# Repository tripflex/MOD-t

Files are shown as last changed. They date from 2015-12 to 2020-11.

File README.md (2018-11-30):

New Matter MOD-t 3d Printer Repo
================================

This repository is a collection of files (firmware, test files, configurations, etc) for the NewMatter MOD-t 3d Printer.

**WARNING:** I take absolutely no responsibility for anything you do with these files or instructions, play at your own risk!

MOD-t's Anonymous
---------------
As of February 28, 2018, New Matter has closed its doors and will no longer be providing WiFi connectivity to the MOD-t through the New Matter Store (will be open until Summer 2018).  A few of us that still enjoy our MOD-t have created a Slack group, please feel free to join us if you need help or want to discuss the future of the MOD-t

Unfortunately New Matter has decided to not release any of the source code for the MOD-t, as well as any software, [stating that there's licensed code they can't release](https://www.reddit.com/r/newmatter/comments/7xly0q/request_for_unewmatter_open_source_modt_firmware/), so instead of providing anything they could without licensed code, they provided nothing ... so time to start reverse engineering, **accepting all applications :)**

[Join the MOD-t Users Slack Channel](https://join.slack.com/t/modt-users/shared_invite/enQtMzM4NzI5Mzg2NDY0LTYxZjUyZTNmNGFjNGZmZmVlOWY5NjNhM2E1MTlhYWY0MTc1YTgyYmMwZGRjNTVmMTI0MGUwNzliYTBmYjVjYmU)

[View NewMatter Subreddit](https://www.reddit.com/r/newmatter/)

[New Matter Closing Blog Post](https://newmatter.com/blog/permanent-closure/)
[Archive.org Cached Version](https://web.archive.org/web/20180301202219/https://newmatter.com/blog/permanent-closure/)

FINAL SOFTWARE WARNINGS
-----------------------
Under the software section you will find a `.dmg` for OSX and `.exe` for Windows that is the last and final software version released by New Matter. **BEWARE** if you install this version **and** upgrade the firmware through the software, this **WILL COMPLETELY DISABLE WIFI ON YOUR MOD-T**

How to print without New New Matter Store
-----------------------------------------
To convert your 3D files into G-code, we recommend two options: Cura, a free software-based slicer, and Astroprint.com, a web-based slicer.

We have prepared a [post on our blog that outlines the entire process for creating G-code with Cura and sending it to your MOD-t through our desktop software application (Web Archive Version)](https://web.archive.org/web/20180301201538/https://newmatter.com/blog/how-to-use-cura-with-the-mod-t/).

[http://www.robosupportsnewmatter.com/blog/how-to-use-cura-with-the-mod-t](http://www.robosupportsnewmatter.com/blog/how-to-use-cura-with-the-mod-t)

Users who prefer not to download and install Cura can continue to “slice” their 3D designs into G-code through a website called Astroprint. This option has the benefit of being web-based, meaning there is no software to download, install, or configure. For a more detailed look at the process for converting your 3D files into G-code using Astroprint, [please see this video](https://www.youtube.com/watch?v=UL1-fpE6NUI).

MOD-t Details
-------------

```
Bed Shape: Rectangular
X Axis: 155.4 mm
Y Axis: 104.6 mm
Z Axis: 130 mm

Nozzle Diameter: 0.4mm
Number of Extruders: 1
Heated Bed: FALSE
```

---

Files
-----

### [`Astroprint.md`](https://github.com/tripflex/MOD-t/tree/master/Astroprint.md)

Information on setting up/configuring Astroprint (with GCode) https://www.astroprint.com/

### [`Basic_GCode.md`](https://github.com/tripflex/MOD-t/tree/master/Basic_GCode.md)

Basic GCode information for setting up the printer (including START and END commands)

### [`clearnozzle.gcode`](https://github.com/tripflex/MOD-t/tree/master/clearnozzle.gcode)

The file `clearnozzle.gcode` is intended to help clear a jammed nozzle on the MOD-t. Just connect your MOD-t to your computer with the USB, launch the MOD-t print tool app and select `Settings > Advanced Mode > Print File`

The MOD-t will do it's little calibration dance and then the nozzle will start to heat to 230ºC (actually it will try, but because the MOD-t is firmware limited to a max temp of 220ºC, it will never get there) and then the print head will move up. The move is just there to indicate that it's gotten to temp. The extruder will then try to push filament through, which should be enough to clear most jams. Finally the print head will move back down and the MOD-t will go back to idle.

---

Directories
-----------

### [Firmware](https://github.com/tripflex/MOD-t/tree/master/firmware)

This directory contains any firmware files I have been able to find, if you have any that are not in the repo, please open an issue or get in contact me with so I can add them.

Go to the directory and see the [Firmware README.md](https://github.com/tripflex/MOD-t/tree/master/firmware) for documentation

### [Slic3r](https://github.com/tripflex/MOD-t/tree/master/Slic3r)

This directory contains configuration files for Slic3r: http://slic3r.org

Launch Slic3r and select `File > Load Config` and select the file

I recommend going in to Preferences in Slic3r and choosing Expert Mode.

### [Cura](https://github.com/tripflex/MOD-t/tree/master/Cura)

Information/Configuration files for Cura https://ultimaker.com/en/products/cura-software

### [Calibration Tests](https://github.com/tripflex/MOD-t/tree/master/Calibration%20Tests)

Settings for the `Extrusion multiplier` in the `Filament Settings` tab of Slic3r, example image, and code to print a single wall.

Go to the directory and see the `README.md` for documentation

### [Scripts](https://github.com/tripflex/MOD-t/tree/master/scripts)

Scripts copied from [Xaero252 Mod-T-Scripts Repo](https://github.com/Xaero252/Mod-T-Scripts) with the exception of `optimize_gcode.py`

`optimize_gcode.py` - is supposed to be the "optimize" from New Matter in the latest version of the software, [quote from reddit](https://www.reddit.com/r/newmatter/comments/7xly0q/request_for_unewmatter_open_source_modt_firmware/):
> Pretty easy to figure out how it works and leads to ~50% smaller gcode files that print much, much faster with much higher print quality.

Go to the directory and see the `README.md` for documentation

### [Lockbar](https://github.com/tripflex/MOD-t/tree/master/Lockbar)

[MOD-Skis: How to Improve the Stability of Your Prints](https://web.archive.org/web/20180619021649/https://newmatter.com/lockbars/)

Includes gcode file and pdf of how to install

---

MOD-t Teardown
-------------
[https://3dprinterwiki.info/newmatter-mod-t/](https://3dprinterwiki.info/newmatter-mod-t/)

[Teardown Pictures](https://flic.kr/s/aHsknFFE6Z)

Resources
---------

-	[MOD-t Reddit](http://www.reddit.com/r/newmatter)
-	[Google MOD-t Group](https://groups.google.com/forum/?#!forum/mod-t)
-	[NewMatter Website](http://www.newmatter.com)
-	[NewMatter MOD-t Support](http://support.newmatter.com)

---

How to contribute
-----------------

If you have a copy of firmware files, update suggestions to configurations, or anything else related to the MOD-t ... please feel free to open a new issue and let me know. I'll be more than happy to update or add anything to this repo.

---

### Credits

The majority of the information and files were obtained from `ajfoul`, make sure to check his repository for any other files or updates he may have added: https://github.com/ajfoul/MOD-t

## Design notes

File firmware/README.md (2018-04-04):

Firmware Upgrade/Downgrade Instructions
---------------------------------------

**WARNING:** I take absolutely no responsibility for anything you do with these files or instructions, play at your own risk!

**WARNING:** Version 1.0.0 will *COMPLETELY DISABLE WIFI* as this is the last release before New Matter closed its doors (see main readme for more info)

To force users to see this warning, the filename will remain `firmware.dfu` and you will need to rename is to `firmware_modt_override.dfu` to flash using instructions below

#### Windows

1.	Download firmware file
2.	Copy `firmware_modt_override.dfu` from the downloaded destination into `C:\firmware_modt_override.dfu`
3.	Run the printer utility and upgrade the FW when prompted.
4.	After FW upload is done look at your About your MOD-t section under the settings section in the printer to check the FW version is X.X.X
5.	Remove/Delete the file under `C:\firmware_modt_override.dfu`

#### MAC OSX (and probably Linux)

1.	Download firmware file
2.	Copy `firmware_modt_override.dfu` from the downloaded destination into `/tmp/firmware_modt_override.dfu`
3.	Run the printer utility and upgrade the FW when prompted.
4.	After FW upload is done look at your About your MOD-t section under the settings section in the printer to check the FW version is X.X.X
5.	Remove/Delete the file under `/tmp/firmware_modt_override.dfu`

**Please follow step 5 or the printer utility will never alert you about updated firmware in the future.**

**Note:** You can also use [dfu-util](http://dfu-util.sourceforge.net) directly from the command line to swap firmware. `dfu-util` is installed by the MOD-t print tool and is what does the actual flashing in automated process above.

On a Mac it's within the app's package:`/Applications/MOD-t\ printer\ tool.app/Contents/MacOS/dfu-util`

On Windows it's located at:`C:\Program Files (x86)\MOD-t\RMbin`

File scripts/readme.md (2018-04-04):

## MOD-t Scripts
Original source from https://github.com/Xaero252/Mod-T-Scripts

##First and foremost:
**USE THESE SCRIPTS AT YOUR OWN RISK!**
These scripts aren't very well tested and almost none of them are completely finished. They work to interface with the printer but it's all very manual.

##Overview and license
This is a basic set of utility scripts to interface with the New Matter Mod-T 3d printer on Linux. You are free to fork and contribute as you see fit.
This work falls under the MIT license. See the LICENSE file for more information.
I must also credit /u/modtdev on reddit for the work on getting the gcode sent to the Mod-T

###Depdencies

1. curl
2. *dfu-util
3. *python3
4. *python3-pyusb

##Usage

First, I recommend creating a udev rule for the Mod-T similar to the following:
/etc/udev/rules.d/51-modt.rules:
    SUBSYSTEM=="usb", ATTR{idVendor}=="2b75", ATTR{idProduct}=="0002", GROUP="users", MODE="0674"
SUBSYSTEM=="usb", ATTR{idVendor}=="2b75", ATTR{idProduct}=="0003", GROUP="users", MODE=0674"

In the above I have everyone in the `users` group enabled, however you can restrict access as needed.
This allows a regular user to run the scripts and still have them operate as intended.

From there most scripts are pretty straightforward. Simply flag them executable and run them. The `send_gcode.py`, `flash_firmware.sh`, and `fw_update.py` are the only scripts requiring arguments, each of them expect a single argument containing the path to an appropriate file for the function requested.  

If you do choose to use these scripts to print things by sending gcode, monitor the output of the `send_gcode.py` script until you see `STATE_JOB_QUEUED` as the printer status. If you press the front panel button prior to seeing this state you will have a broken print job, which will not print correctly.

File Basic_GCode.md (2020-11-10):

Basic GCode
===========

Here are the basic GCode start and end commands for the MOD-t ... check the other configuration files for more information.

### START commands:

```
M42 P10 S1 ; Turn on LED
G21 ; set units to millimeters
G90 ; use absolute coordinates
M82 ; use absolute distances for extrusion
M204 S500

G0 Z1 F300 ; Make sure main Z drop isn’t too fast

;Move to side and put down a line to prime the nozzle
G1 X64.332 Y24.938 F9000
G1 Z0.315 F300
G92 E0
G1 X74.332 Y-44.938 E3.9642 F2520
G1 X74.964 Y-44.938 E4.0001
G1 X74.964 Y24.938 E7.9643
G1 X74.532 Y24.938 E7.9888
G1 X74.332 Y24.938 F2520
G1 X73.876 Y25.394 F9000
G92 E0
G1 X73.876 Y-45.394 E4.0159 F1680
G1 X75.42 Y-45.394 E4.1035
G1 X75.42 Y25.394 E8.1195
G1 X74.076 Y25.394 E8.1957
G1 X73.876 Y25.394 F1680
G1 X73.876 Y23.394 F1680

G0 Z1 F300
G0 X0 Y0 F5000

G92 E0
```

### END commands:

```
G92 E0
G0 Z130 F300; Go high

G0 X77.7 Y52.3 F3000
G92 X0 Y0 ; Change Offset back to center

G0 X0 Y50 F3000; Go front and center
M104 S0 ; Turn off temperature
M107 ; Turn on fan
M84 ; Disable motors
```

Original Source: http://support.newmatter.com/customer/portal/questions/14427572-how-do-change-print-settings-like-infill-support-etc-

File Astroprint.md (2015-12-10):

Astroprint Configuration
========================

If you are using Astroprint to create G-Code from .OBJ and .STL files you've designed in a CAD program here are the settings for the MOD-t printer you need to set up a customer printer in Astroprint:

### Basic Details

```
Bed Shape: Rectangular
X Axis: 155.4 mm
Y Axis: 104.6 mm
Z Axis: 130 mm

Nozzle Diameter: 0.4mm
Number of Extruders: 1
Heated Bed: Toggle Off
```

### Advanced Settings:

```
Slicing Software: Cura
Print File Format: gcode
gcode Flavor: RepRap
```

### Start Commands:

```
M42 P10 S1 ; Turn on LED
G21 ; set units to millimeters
G90 ; use absolute coordinates
M82 ; use absolute distances for extrusion
M204 S500

G0 Z1 F300 ; Make sure main Z drop isn’t too fast

;Move to side and put down a line to prime the nozzle
G1 X64.332 Y24.938 F9000
G1 Z0.315 F300
G92 E0
G1 X74.332 Y-44.938 E3.9642 F2520
G1 X74.964 Y-44.938 E4.0001
G1 X74.964 Y24.938 E7.9643
G1 X74.532 Y24.938 E7.9888
G1 X74.332 Y24.938 F2520
G1 X73.876 Y25.394 F9000
G92 E0
G1 X73.876 Y-45.394 E4.0159 F1680
G1 X75.42 Y-45.394 E4.1035
G1 X75.42 Y25.394 E8.1195
G1 X74.076 Y25.394 E8.1957
G1 X73.876 Y25.394 F1680
G1 X73.876 Y23.394 F1680

G0 Z1 F300
G0 X0 Y0 F5000

G92 X77.7 Y52.3 ; Offset Origin from center to top right corner to accommodate Astroprint requirement
G92 E0
```

### End Commands:

```
G92 E0
G0 Z130 F300; Go high

G0 X77.7 Y52.3 F3000
G92 X0 Y0 ; Change Offset back to center

G0 X0 Y50 F3000; Go front and center
M104 S0 ; Turn off temperature
M107 ; Turn on fan
M84 ; Disable motors
```

Original Source: http://support.newmatter.com/customer/en/portal/articles/2131173-what-settings-should-i-use-for-astroprint-

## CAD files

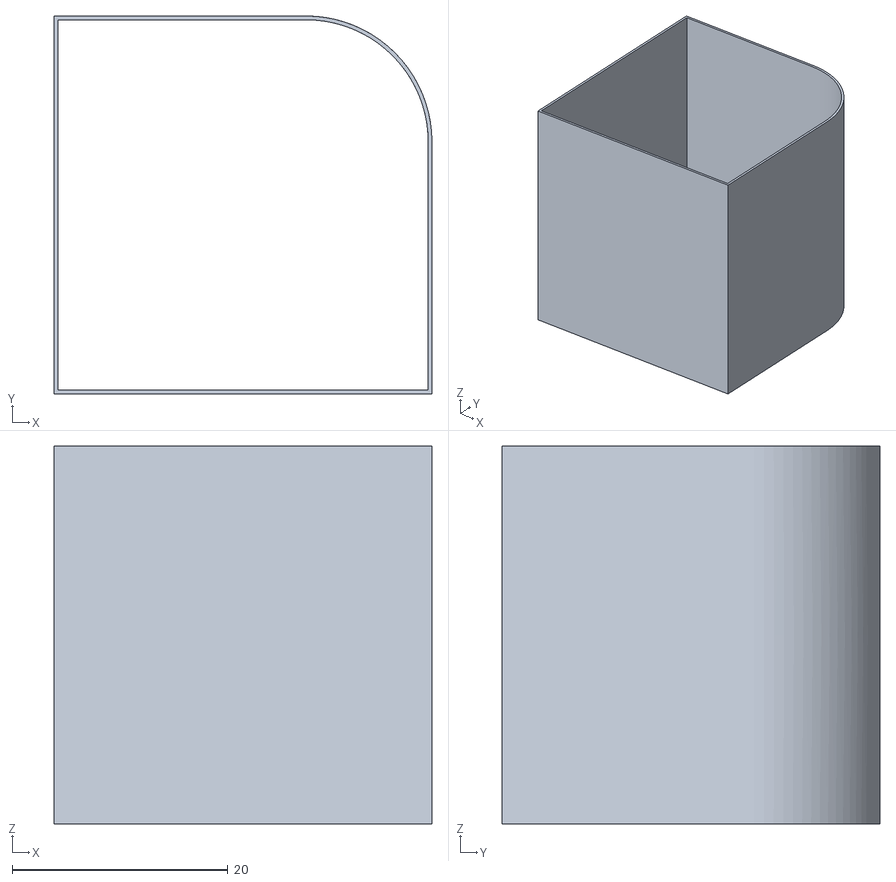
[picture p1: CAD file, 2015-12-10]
Calibration Tests/singlewallcalibration35.stl
35.0 x 35.0 x 35.0

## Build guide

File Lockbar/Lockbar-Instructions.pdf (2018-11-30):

### Build Tray Lockbar fabrication and installation instructions

31 Jan 2017

Step 1 – Print the lockbars

Print the “Lockbar 2x.gcode” file by sending it via USB with the MOD-t desktop app. This will print two of the "lockbars" in one print job, as you'll need two per MOD-t you want to modify.

Step 2 – Clean up the prints

Carefully remove the supports that are printed in the small cavities at either end of the bar. I found that an x-acto knife or razor blade works best for this, as the fit is important so you'll want to make sure there are no support remnants remaining in the wedge-shaped cavity.

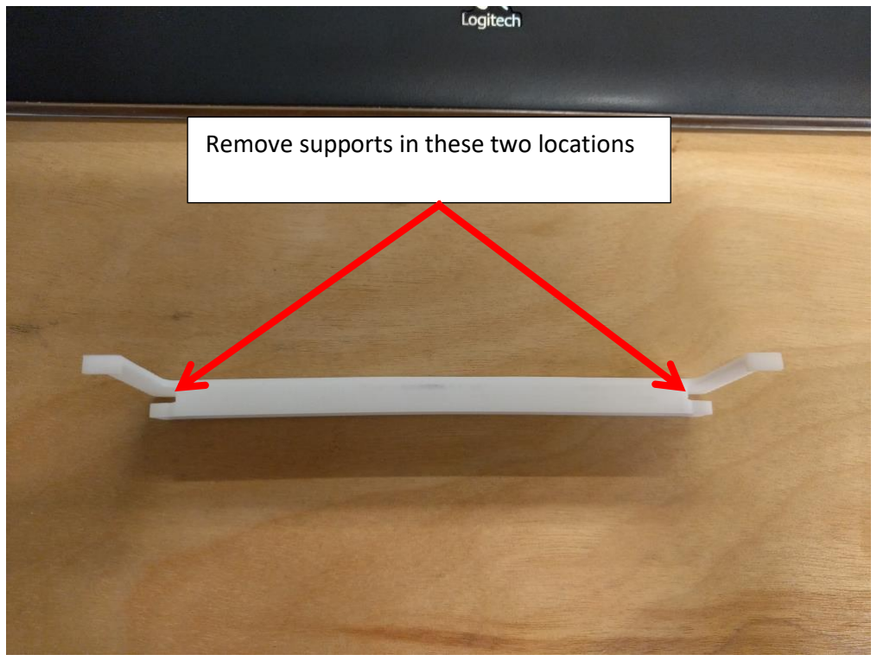
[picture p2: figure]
Remove supports in these two locations
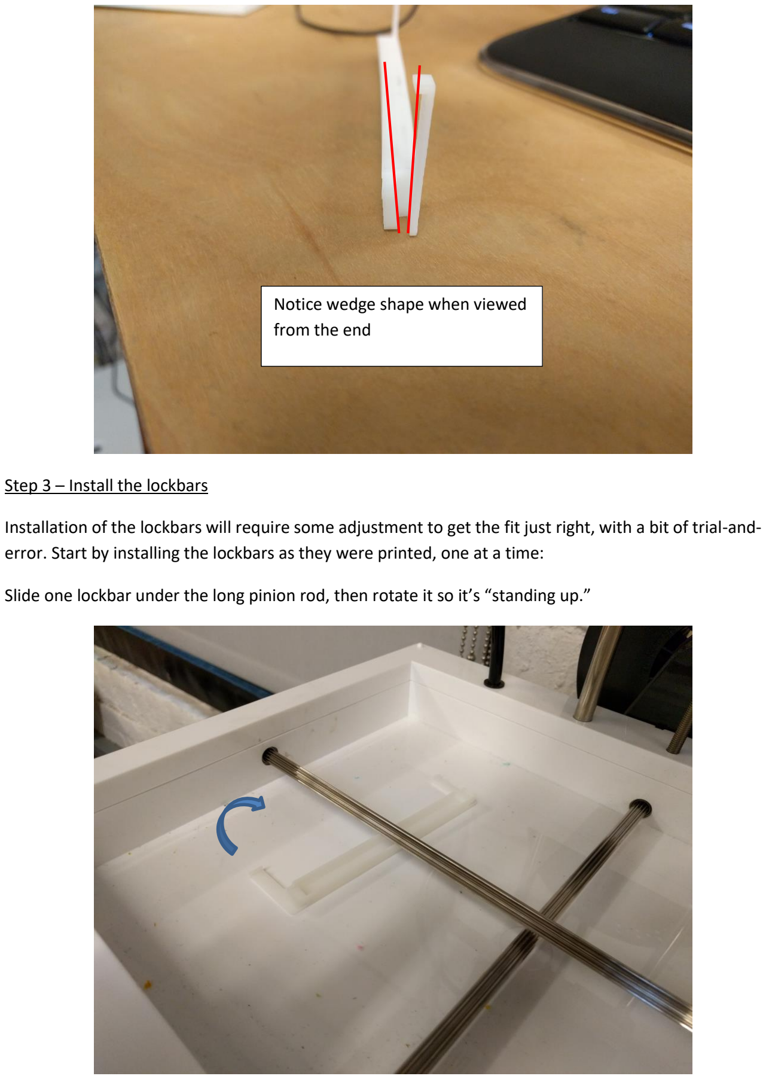
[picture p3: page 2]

Step 3 – Install the lockbars

Installation of the lockbars will require some adjustment to get the fit just right, with a bit of trial-anderror. Start by installing the lockbars as they were printed, one at a time:

Slide one lockbar under the long pinion rod, then rotate it so it’s “standing up.”

Notice wedge shape when viewed from the end

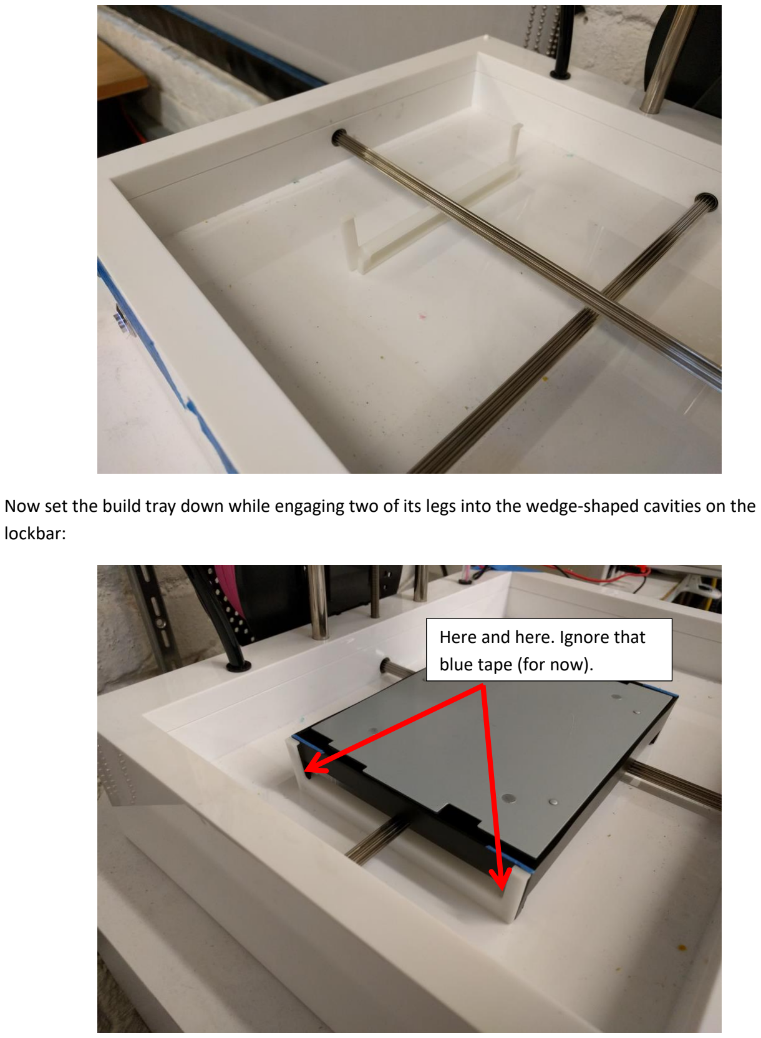
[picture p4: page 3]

Now set the build tray down while engaging two of its legs into the wedge-shaped cavities on the lockbar:

Here and here. Ignore that blue tape (for now).

Provide some upward tension on the lockbar to get the fingers to latch over the top edge of the build tray:

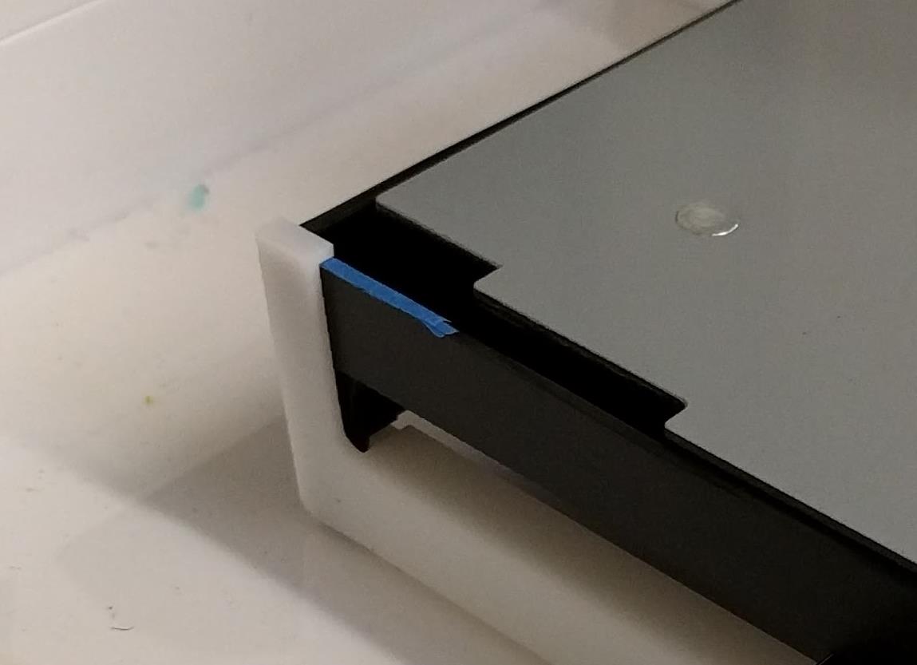
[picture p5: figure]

Now repeat with the other one, taking care to ensure the build tray is properly aligned on the pinion rod while doing so. I recommend performing the second installation with the tray at the end of its x-axis travel, allowing you to use the short pinion rod and the side of the MOD-t’s base as alignment references:

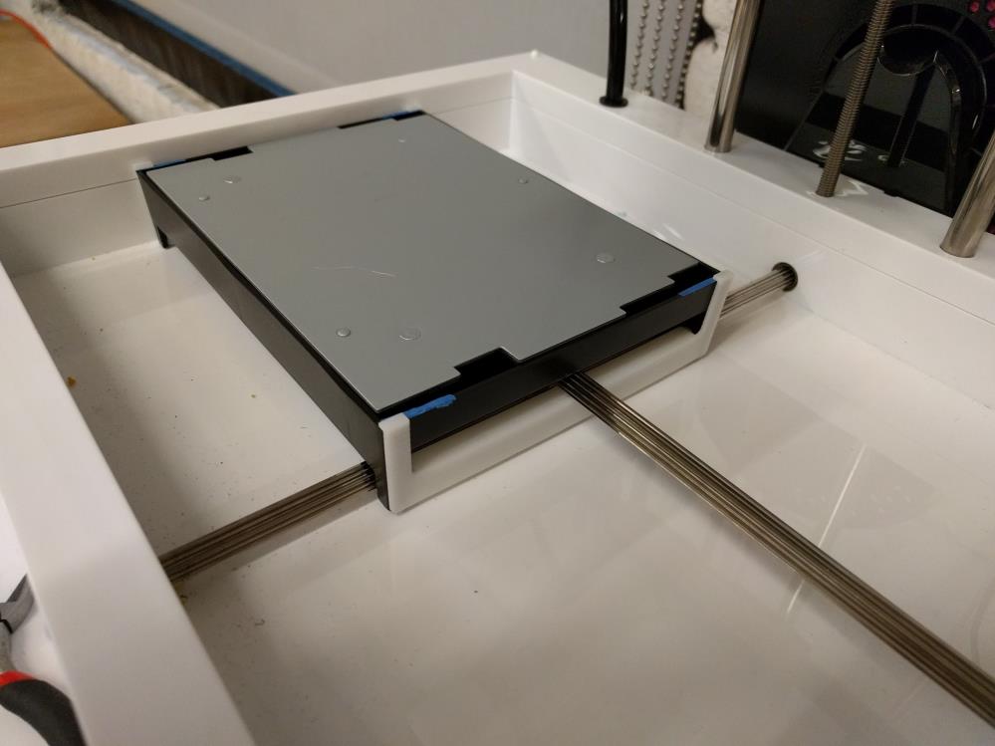
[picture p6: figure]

Step 4 – Test the fit and adjust the lockbars

In order to operate correctly, the lockbars must be positioned such that they prevent the pinion rod from disengaging with the gear teeth on the build tray. To test this after installing the lockbars, provide some gentle upward force on one end of the build tray and test whether you’re able to slide it forwardand-back over the pinion rod without the pinion rod turning. If so, then the lockbar is too loose. Test this on both sides.

Should one or both lockbars be too loose, you’ll need to first uninstall it (following the reverse of the installation procedure above) and add some shims to the top surface of the build tray, where the lockbar fingers interface with it. In my example case, I’ve used narrow strips of blue painter’s tape which I cut to size with a razor, visible in the images above.

Once you’ve added some shims, re-install the lockbars and test the fit again. This may require several repetitions to get the fit just right. The proper fit will (a) prevent disengagement of the build tray gear teeth from the pinion rod, and (b) allow free, unrestricted rotation of the pinion rod to drive the build tray.

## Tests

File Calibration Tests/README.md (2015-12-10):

MOD-t Calibration Tests
=======================

Singlewallcalibration35.stl is for use in setting the the 'Extrusion multiplier' in the 'Filamnet Settings' tab of Slic3r as documented here: https://github.com/alexrj/Slic3r/wiki/Calibration (There is a an STL file there that can also be used.)

I've provided Singlewallcalibration35.gcode which has been sliced with the MOD-t_slic3r_config.ini settings as a convenience for those who may have not yet installed Slic3r and would just like to try printing a single wall part.

Singlewallcalibration35.png is a rendering of the part for reference.

The part is a 35x35x35mm cube with one edge at a 11.667mm (35mm/3) radius.

Original Source: https://github.com/ajfoul/MOD-t

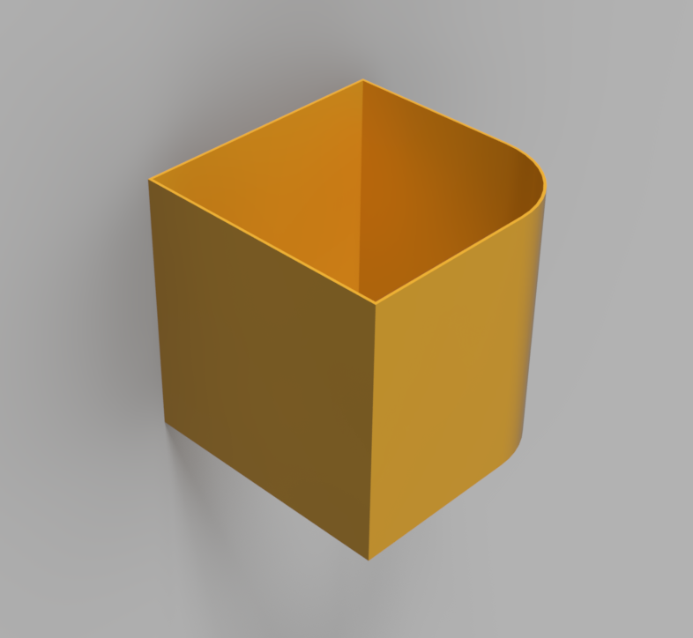
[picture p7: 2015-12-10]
Calibration Tests/singlewallcalibration35.png

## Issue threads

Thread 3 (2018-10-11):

Question: Polarity of Mod-T power supply

wizard23, 2018-10-11:
Hi, sorry to post this question here: Can anybody who owns a mod-t meaure the power supply and tell me if plus is on the inside or the outside of the connector? I lost the power supply and need to replace it but I dont want to fry it...

rokhead, 2018-10-13:
inside is positive, outside is ground.
24v DC, 2.5A output

wizard23, 2018-10-13:
kthnx!

Closed 2018-10-13.

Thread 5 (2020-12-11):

Windows cannot find exe

ehernan3, 2020-12-11:
A friend has given me their Mod-t printer. I then learned that NewMatter has closed, so I found your git repo, and downloaded MOD-t-FINAL-DISABLES-WIFI.exe from this repo. I'm trying to run this on my Windows 10 laptop.

When I double click the file, a window pops up "This app can't run on your PC. To find a version for your PC, check with the software publisher".

When I Run as administrator, I get the following message, which contradicts my file system:
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

Is this software not compatible with Windows 10?

tripflex, 2020-12-13:
Download looks corrupted, it should be almost 50mb in size, try downloading with a different browser

ehernan3, 2020-12-13:
@tripflex , this issue is resolved. What I had done earlier was RMB Save As on the exe file so I could choose the destination directory. That apparently doesn't work in Git, so(using the same browser as before, Chrome) I clicked on the file to expose the Download button, which works flawlessly.

You were totally correct that the original Save As download was corrupted. Click on the file first shows that it is indeed 43Mb, yet Save As corrupts that into 100k. Shame on me for not noticing that.

Hmm, I didn't know that about Git. I use it at work, but at work, I never 'download' stuff. I'm always following the normal Gitflow(cloning, committing, pushing, merging, etc). This is the first time I've tried to use Git outside the normal flow.

tripflex, 2020-12-13:
Awesome thanks for the update, best of luck!

Closed 2020-12-13.

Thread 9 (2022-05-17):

Question

emani0816, 2022-05-17:
I'm not sure this is the correct place to leave this question but I don't see another place.   I am a teacher at a middle school that currently owns three MOD-t printers.  Unfortunately the computers that previously controlled them have been lost and we are left with three printers with no software.  I happened upon this website but I am unsure how to transform the pages of code into a program so I can once again use these printers.  Any help you can offer would be greatly appreciated.

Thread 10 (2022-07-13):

Making it work

tiny102, 2022-07-13:
I have been trying to get this to work with MOD-T but it seems not to recognize it as it is plugged in via cable. I have even tried the one with WIFI disabled but that still has not worked. Is there something that I'm missing when installing the application or should I not even try to get it to work again

GeneTognetti, 2022-07-14:
Not sure what to suggest. Did you try the How to print without New Matter section? Good luck!

GeneTognetti, 2022-07-14:
I was able to get mine to work following the instructions on this page -
but that was several years ago. I suggest you really look through what is
in the MOD-t group. That's what helped me. I don't know what else to
suggest. Good luck!

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

tiny102, 2022-07-14:
OK thank you so much for that info

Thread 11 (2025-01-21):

Documentation of the mystery packet in the Mod-T scripts

acuteaangle, 2025-01-21:
Hello! I’m not really sure where to put this, but I wanted to write it down somewhere in case anyone else comes across this looking for an answer.

The Mod-T scripts include several lines like the following:
```python
# Some commands are human readable some are maybe checksums
dev.write(2, bytearray.fromhex('246a0095ff'))
dev.write(2, '{"transport":{"attrs":["request","twoway"],"id":3},"data":{"command":{"idx":0,"name":"bio_get_version"}}};')
```

The mystery packet seems to consist of the fixed bit pattern 0x24[^1], followed by the 2-byte, little-endian length of the message, and then that same 2-byte length inverted (bitwise not).

Here is my implementation in Rust, which matches for every sample in the scripts.
```rust
fn compute_prefix_packet(message: &str) -> [u8; 5] {
    const FIXED_PREFIX: u8 = 0b_0010_0100;
    let length: [u8; 2] = { message.len() as u16 }.to_le_bytes();
    return [FIXED_PREFIX, length[0], length[1], !length[0], !length[1]];
}
```

[^1]: It is, of course, possible that this value actually contains meaning. However, unlike the probably little-endian 0x00 and 0xFF bytes, I think this is most likely just a bit pattern intended to help prevent the beginning of a front-turncated message being misinterpreted as the length.

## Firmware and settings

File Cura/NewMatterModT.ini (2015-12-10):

[machine]
machine_name = New Matter Mod-T
machine_type = reprap
machine_width = 155.4
machine_depth = 104.6
machine_height = 130
machine_center_is_zero = True
machine_shape = Square
ultimaker_extruder_upgrade = False
has_heated_bed = False
gcode_flavor = RepRap (Marlin/Sprinter)
extruder_amount = 1
extruder_offset_x1 = 0.0
extruder_offset_y1 = 21.6
extruder_offset_x2 = 0.0
extruder_offset_y2 = 0.0
extruder_offset_x3 = 0.0
extruder_offset_y3 = 0.0
extruder_offset_x4 = 0.0
extruder_offset_y4 = 0.0
steps_per_e = 0
serial_port = AUTO
serial_port_auto =
serial_baud = AUTO
serial_baud_auto =
extruder_head_size_min_x = 0
extruder_head_size_min_y = 0
extruder_head_size_max_x = 0
extruder_head_size_max_y = 0
extruder_head_size_height = 0

[profile]
layer_height = 0.2
wall_thickness = 1.2
retraction_enable = True
solid_layer_thickness = 0.3
fill_density = 25
print_speed = 60
print_temperature = 210
print_temperature2 = 0
print_temperature3 = 0
print_temperature4 = 0
print_temperature5 = 0
print_bed_temperature = 70
support = Everywhere
platform_adhesion = None
support_dual_extrusion = Both
wipe_tower = False
wipe_tower_volume = 15
ooze_shield = False
filament_diameter = 1.75
filament_diameter2 = 0
filament_diameter3 = 0
filament_diameter4 = 0
filament_diameter5 = 0
filament_flow = 100.0
nozzle_size = 0.4
retraction_speed = 150
retraction_amount = 1.5
retraction_dual_amount = 16.5
retraction_min_travel = 1.5
retraction_combing = All
retraction_minimal_extrusion = 0.02
retraction_hop = 0.0
bottom_thickness = 0.3
layer0_width_factor = 100
object_sink = 0.0
overlap_dual = 0.15
travel_speed = 80.0
bottom_layer_speed = 30
infill_speed = 60
solidarea_speed = 0.0
inset0_speed = 30
insetx_speed = 40
cool_min_layer_time = 5
fan_enabled = True
skirt_line_count = 1
skirt_gap = 3.0
skirt_minimal_length = 150.0
fan_full_height = 0
fan_speed = 100
fan_speed_max = 100
cool_min_feedrate = 10
cool_head_lift = False
solid_top = True
solid_bottom = True
fill_overlap = 15
perimeter_before_infill = False
support_type = Lines
support_angle = 60
support_fill_rate = 15
support_xy_distance = 0.7
support_z_distance = 0.25
spiralize = False
simple_mode = False
brim_line_count = 20
raft_margin = 5.0
raft_line_spacing = 3.0
raft_base_thickness = 0.3
raft_base_linewidth = 1.0
raft_interface_thickness = 0.27
raft_interface_linewidth = 0.4
raft_airgap_all = 0.0
raft_airgap = 0.22
raft_surface_layers = 2
raft_surface_thickness = 0.27
raft_surface_linewidth = 0.4
fix_horrible_union_all_type_a = True
fix_horrible_union_all_type_b = False
fix_horrible_use_open_bits = False
fix_horrible_extensive_stitching = False
plugin_config =
object_center_x = -1
object_center_y = -1
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

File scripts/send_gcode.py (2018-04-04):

#!/usr/bin/env python

# USAGE: send_gcode.py file.gcode
# Requires read/write permission to the Mod-T via USB.

import sys
import os
import usb.core
import usb.util
import time
from zlib import adler32

# Adler32 checksum function 
# Based on https://gist.github.com/kofemann/2303046
# For some reason, mod-t uses 0, not 1 as the basis of the adler32 sum
BLOCKSIZE=256*1024*1024

def adler32_checksum(fname):
 asum = 0 
 f = open(fname, "rb")
 while True:
   data = f.read(BLOCKSIZE)
   if not data:
        break
   asum = adler32(data, asum)
   if asum < 0:
        asum += 2**32
 f.close()
 return asum

# Read pending data from MOD-t (bulk reads of 64 bytes)
def read_modt(ep):
 text=''.join(map(chr, dev.read(ep, 64)))
 fulltext = text
 while len(text)==64:
        text=''.join(map(chr, dev.read(ep, 64)))
        fulltext = fulltext + text
 return fulltext

# Main program
if __name__ == '__main__':

    if not len(sys.argv)==2:
        print("Usage: send_gcode.py filename.gcode")
        quit()

# Read filename argument and check that the file exists
fname=str(sys.argv[1])
if not os.path.isfile(fname):	
	print(fname + " not found")
	quit()

# Get the size of the gcode file
size = os.path.getsize(fname)

# Get the adler32 checksum of the gcode file
checksum=adler32_checksum(fname)

# Open gcode file and read into buffer
f = open(fname, "rb")
gcode = f.read()
f.close()

# Find MOD-t usb device
dev = usb.core.find(idVendor=0x2b75, idProduct=0x0002)

# was it found?
if dev is None:
    raise ValueError('Device not found')

# set the active configuration. With no arguments, the first
# configuration will be the active one
dev.set_configuration()

# These came from usb dump. 
# Some commands are human readable some are maybe checksums 
dev.write(2, bytearray.fromhex('246a0095ff'))
dev.write(2, '{"transport":{"attrs":["request","twoway"],"id":3},"data":{"command":{"idx":0,"name":"bio_get_version"}}};')
print(read_modt(0x81))

dev.write(4, '{"metadata":{"version":1,"type":"status"}}')
print(read_modt(0x83))

dev.write(2, bytearray.fromhex('248b0074ff'))
dev.write(2, '{"transport":{"attrs":["request","twoway"],"id":5},"data":{"command":{"idx":22,"name":"wifi_client_get_status","args":{"interface_t":0}}}};')
print(read_modt(0x81))

dev.write(2, bytearray.fromhex('246a0095ff'))
dev.write(2, '{"transport":{"attrs":["request","twoway"],"id":7},"data":{"command":{"idx":0,"name":"bio_get_version"}}};')
print(read_modt(0x81))

dev.write(4, '{"metadata":{"version":1,"type":"status"}}')
print(read_modt(0x83))

dev.write(4, '{"metadata":{"version":1,"type":"status"}}')
print(read_modt(0x83))

# Start writing actual gcode
# File size and adler32 checksum calculated earlier
dev.write(4, '{"metadata":{"version":1,"type":"file_push"},"file_push":{"size":'+str(size)+',"adler32":'+str(checksum)+',"job_id":""}}')

# Write gcode in batches of 20 bulk writes, each 5120 bytes. 
# Read mod-t status between these 20 bulk writes

start=0
counter=0
while True:
 if (start+5120-1>size-1):
        end=size
 else:
        end=start+5120
 block = gcode[start:end]
 print(str(counter)+':' +str(start)+'-'+str(end-1)+'\t'+str(len(block)))
 counter += 1
 if counter>=20:
  temp=read_modt(0x83)
  counter = 0
 dev.write(4, block)
 if (start == 0):
  temp=read_modt(0x83)
 start = start + 5120
 if (start>size):
        break;

# Gcode sent. Finally, loop and query mod-t status every 5 seconds 
while True:
 dev.write(4, '{"metadata":{"version":1,"type":"status"}}')
 print(read_modt(0x83))
 time.sleep(5)

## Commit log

2015-12-10 initial push
    [singlewallcalibration35.stl]
2018-04-04 add how to print without store
